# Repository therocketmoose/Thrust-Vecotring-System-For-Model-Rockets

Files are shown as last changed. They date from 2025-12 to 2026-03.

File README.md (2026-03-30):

Thrust Vectoring & Landing Control System for Model Rockets

Lead Engineer: Xavier Vimard
Project Start: 27/09/2025
Expected Completion: 20/05/2026

Project Overview:

This repository contains the full development of a thrust-controlled landing system (TCLS) for a model rocket platform. The project aims to design, build, and test a reusable model rocket capable of performing controlled ascent, attitude stabilization, descent management, and soft landing. The objective is to create a working proof-of-concept that integrates thrust vectoring, aerodynamic control, reaction wheel stabilization, and deployable landing legs into a unified flight system. This project is expected to operate over a one-year development window, with several intermediate prototypes and test campaigns.

The rocket platform itself is not the primary focus, the emphasis is the TCLS hardware, control algorithms, and validation testing necessary to achieve reliable vertical landing.



Project Goals:
- Develop a fully functional thrust vectoring system capable of four-axis gimbal control for ascent and landing.

- Implement a stability assist system using grid fins to manage minor deviations during ascent.

- Design a reaction wheel to counter roll and maintain thrust vector orientation.
as roll stabilization is critical, as uncontrolled roll makes TVC ineffective.

- Engineer deployable landing legs to ensure stable recovery after touchdown.

- Build a complete electronics and software stack integrating sensors, control logic, and closed-loop PID stabilization.

- Validate feasibility via simulation, static fire testing, and full-scale launch tests.

Development Timeline:

My project follows a structured month-by-month roadmap:

- Nov 2025: Design, print and stress test the TVC mount, the reaction wheel and the payload bay.
- Dec 2025: Design and simulate and prepare the code for the PCB.
- Jan 2026: Test the TVC with real motors, sssemble prototype rocket (without parachute), refine TVC mount, begin full system dry runs.
- Feb 2026: First flight test of the prototype, collect IMU/GPS data, evaluate control authority.
- Mar 2026: Analyze flight performance, improve PID tuning, begin landing system integration.
- Apr 2026: Integrate final landing mechanism, conduct ground validations.
- May 2026: Perform full integration test and finalize launch preparation for main flight.
- Jun 2026: Full-system launch and documentation of results.

System Architecture
Core Components:

- MCU: Teensy 4.1 — selected for deterministic real-time control performance.

- IMU: Bosch BMI088 — optimized for high-vibration flight profiles.

- Barometer: MS5611 — high-resolution altitude tracking (10 cm).

- Ground Sation: ESP32 and Lora reciever — supplementary system for communication and logging.

- Structure: Carbon fiber body, TVC gimbal, electronics bay, reaction wheel assembly.



CAD & Mechanical: 
The CAD design includes

- A 4-axis servo-driven TVC module.

- A compact reaction-wheel chamber below the nose cone.

- A payload bay positioned directly above the TVC to avoid cable latency.



Simulation Work

To validate feasibility, ascent and landing behavior is simulated using Xcos (SciLab).
Simulations include gyro stabilization behavior, ascent velocity and altitude curves, and TVC response testing. Early results indicate stable linear altitude growth and adequate thrust-to-weight margin, confirming the motor’s suitability for controlled ascent.



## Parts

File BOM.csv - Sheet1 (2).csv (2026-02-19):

CPN | Part Name | Qty | Source | Mfg Part # | Price | Link
10-2001 | Teensy 4.1 Development Board | 1 | AliExpress | TEENSY41 | 47.59 | https://www.aliexpress.com/w/wholesale-Teensy-4.1-development-board.html
30-0001 | TSP F35-p Rocket Engine (Pack of 2) | 2 | SierraFox | F35-P | 72.5 | https://www.sierrafoxhobbies.com/en/2439-f35-p-single-use-tsp-29-mm-model-rocket-engine-2-pcs.html
20-0001 | BMI088 Shuttle Board | 1 | Mouser | BMI088-SB | 13.67 | https://www.mouser.es/ProductDetail/Bosch-Sensortec/BMI088-Shuttle-Board-30
20-0002 | MS5611 Barometric Pressure Sensor | 1 | ManoMano | MS5611-01BA03 | 7.87 | https://www.manomano.es/componentes-electronicos-4189
20-0003 | LoRa Module SX1278 (433MHz) | 1 | AliExpress | SX1278 | 2.33 | https://www.aliexpress.com/item/1005001593805902.html
30-0002 | 5V DC Motor (Hobby Type) | 1 | AliExpress | Generic | 0.99 | https://www.aliexpress.com/w/wholesale-5v-dc-motor.html
30-0003 | 9g Micro Servo (SG90) (5pcs) | 1 | AliExpress | SG90 | 9.49 | https://www.aliexpress.com/item/32425569444.html
30-0004 | 5g Micro Servo (GH-S37D) | 1 | AliExpress | GH-S37D | 2.89 | https://www.aliexpress.com/item/1005005335388228.html
10-2002 | ESP32-WROOM-32 Dev Module | 1 | AliExpress | ESP32-WROOM | 2.24 | https://es.aliexpress.com/item/1005006096278268.html
20-0004 | SX1278 LoRa Receiver (868MHz) | 1 | AliExpress | SX1276 | 10.59 | https://www.amazon.es/cart/smart-wagon?newItems=9bc834af-a09a-47e9-a199-14235897edb9,1
20-0005 | LoRa/RF Antenna (SMA 868MHz) | 1 | AliExpress | Generic | 1.82 | https://www.aliexpress.com/item/1005002863723277.html
40-0001 | Custom Carbon Fiber Tubes (Est.) | 1 | Custom | Custom | 70 | N/A

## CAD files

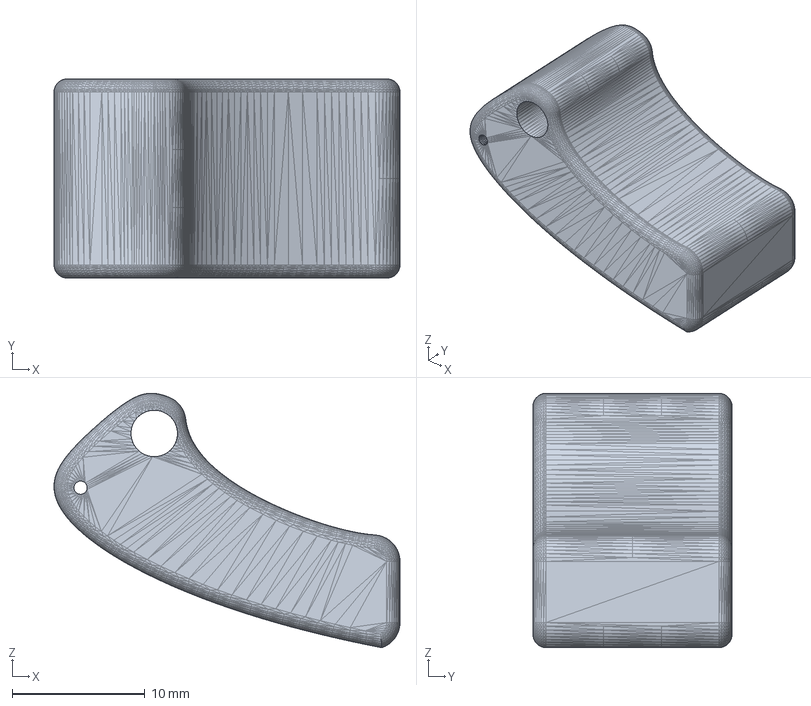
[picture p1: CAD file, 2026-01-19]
3D printing files (TVC)/Thrust arm L.step
26.0 x 15.0 x 19.2 mm

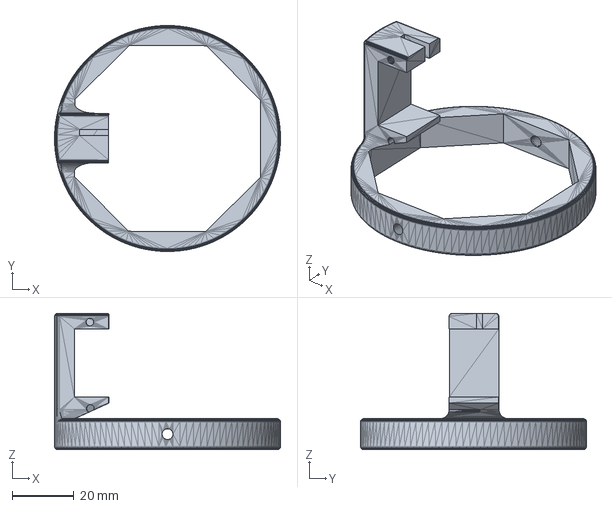
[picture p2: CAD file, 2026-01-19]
3D printing files (TVC)/Outer Gimbal.step
73.0 x 73.0 x 44.0 mm

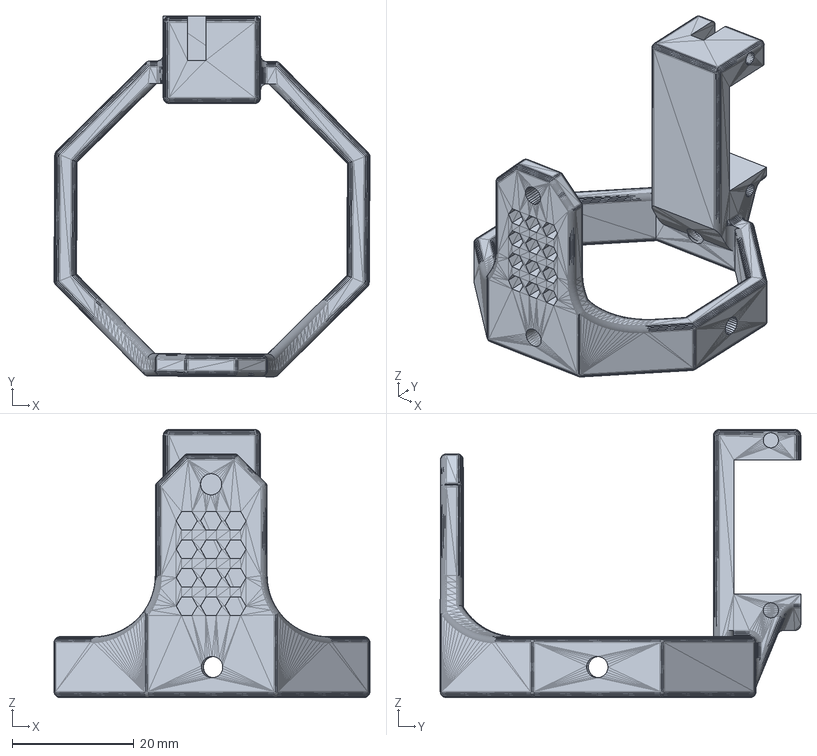
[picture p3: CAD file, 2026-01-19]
3D printing files (TVC)/Inner Gimbal.step
51.9 x 59.2 x 44.0 mm

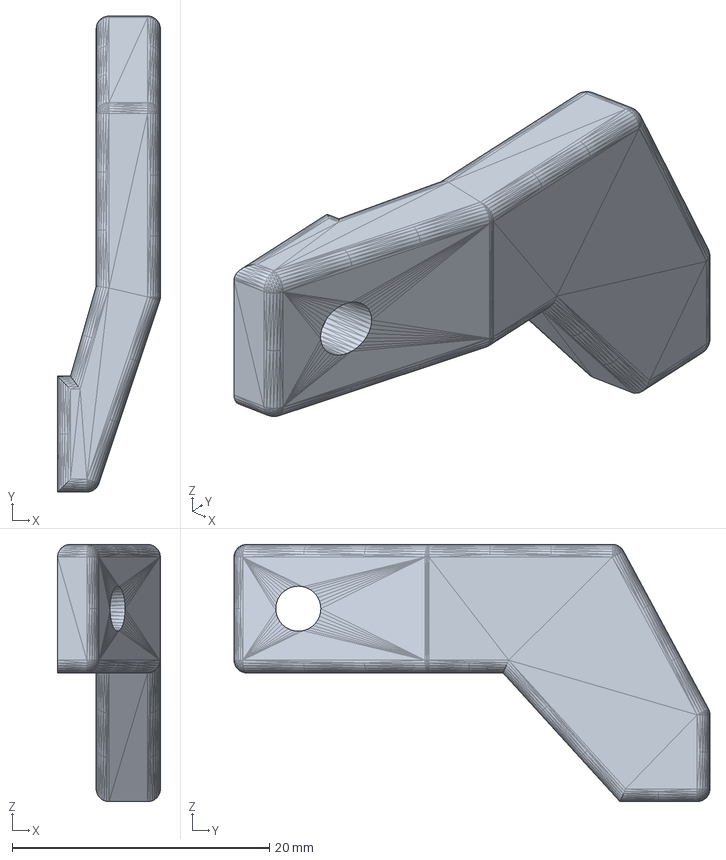
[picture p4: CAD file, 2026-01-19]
3D printing files (TVC)/Pitch Servo Arm.step
8.00 x 37.0 x 20.0 mm

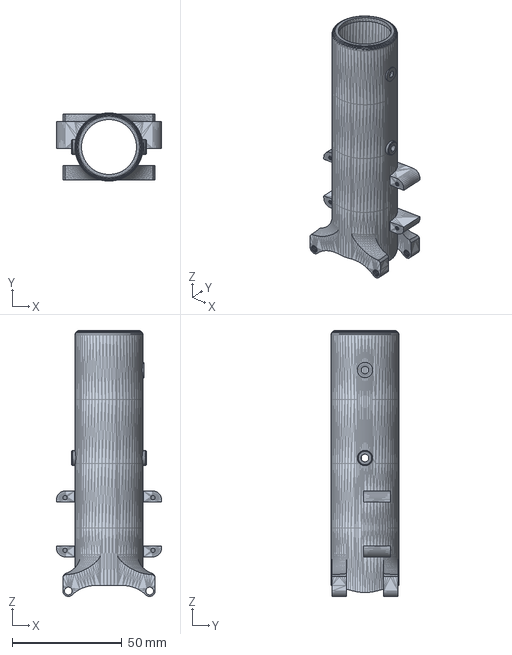
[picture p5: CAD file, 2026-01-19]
3D printing files (TVC)/Motor tube.step
47.9 x 31.0 x 121.0 mm

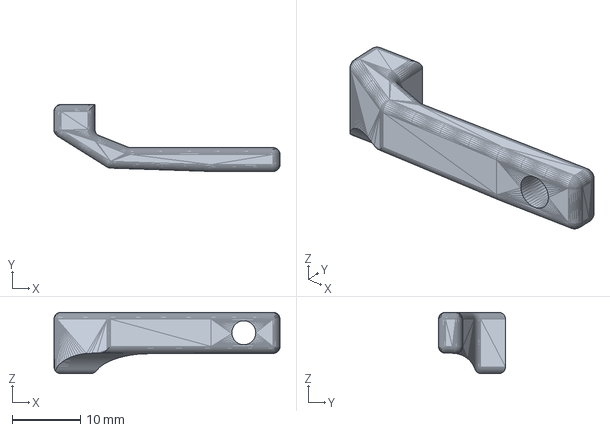
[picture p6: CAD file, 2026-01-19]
3D printing files (TVC)/Yaw Servo Arm.step
33.1 x 9.81 x 9.00 mm

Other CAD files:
3D printing files (TVC)/Thrust arm R.step

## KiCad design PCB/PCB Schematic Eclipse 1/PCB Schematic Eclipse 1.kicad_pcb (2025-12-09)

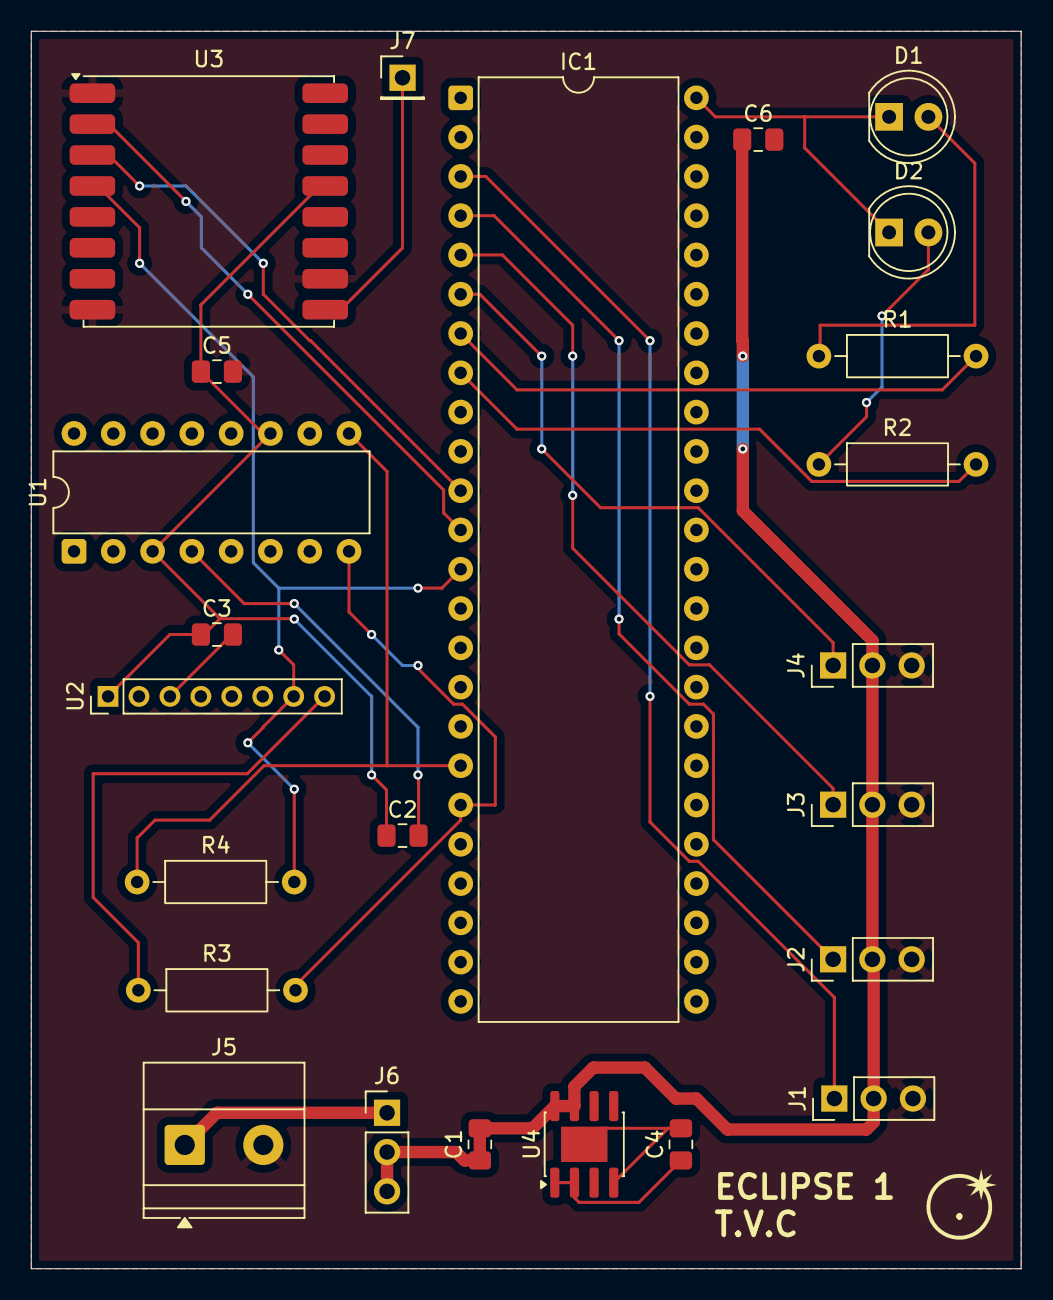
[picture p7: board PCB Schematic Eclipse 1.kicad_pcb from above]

Board: 2 copper layers, 64.0 x 80.0 mm, 25 parts (0 on the bottom side), 24 nets.

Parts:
.: LOGO
C1, C4: C_Polarized; C_0805_2012Metric_Pad1.18x1.45mm_HandSolder
C2, C3, C5, C6: C; C_0805_2012Metric_Pad1.18x1.45mm_HandSolder
D1, D2: LED; LED_D5.0mm
IC1: TEENSY_4.1; DIP-48_W15.24mm
J1, J2, J3, J4, J6: Conn_01x03; PinHeader_1x03_P2.54mm_Vertical
J5: Conn_01x02_Pin; TerminalBlock_Phoenix_MKDS-1,5-2-5.08_1x02_P5.08mm_Horizont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
J7: Conn_01x01_Pin; PinHeader_1x01_P2.54mm_Vertical
R1, R2, R3, R4: R; R_Axial_DIN0207_L6.3mm_D2.5mm_P10.16mm_Horizontal
U1: BMI088; DIP-16_W7.62mm
U2: MS5611-01BA03; PinHeader_1x08_P2.00mm_Vertical
U3: RFM95W-868S2; HOPERF_RFM9XW_SMD
U4: ADP7142ARDZ-3.3; SOIC-8-1EP_3.9x4.9mm_P1.27mm_EP2.29x3mm

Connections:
/I2C_SCL: IC1.19 (A5), R3.2, U1.8 (SCL/SCK)
/I2C_SDA: IC1.18 (A4), R4.1, U1.9 (SDA/SDI)
/SPI_MISO: IC1.12 (MISO), U3.2 (MISO)
/SPI_MOSI: IC1.11 (MOSI), U3.3 (MOSI)
/SPI_SCK: IC1.13 (SCK), R4.2, U2.7 (SDI/SDA), U3.4 (SCK)
/VCC_3V3: C2.1, C3.1, C5.1, U1.3 (VDD), U1.11 (VDDIO), U2.1 (VDD), U3.13 (3_3V)
/Vcc_3V3: C4.1, U4.1 (VOUT), U4.2 (VOUT)
GND: C5.2, J1.3, J2.3, J3.3, J4.3, J5.2, U3.1 (GND), U3.8 (GND@1), U3.10 (GND@2)
unnamed: C4.2, U4.4 (GND), U4.9 (GND)
unnamed: D1.2 (A), R1.1
unnamed: D1.1 (K), D2.1 (K), IC1.48 (GND_2)
unnamed: D2.2 (A), R2.1
unnamed: IC1.4 (BCLK2), J2.1
unnamed: IC1.5 (IN2), J3.1
unnamed: IC1.3 (LRCLK2), J1.1
unnamed: IC1.6 (OUT1D), J4.1
unnamed: IC1.7 (RX2), R1.2
unnamed: IC1.8 (TX2), R2.2
unnamed: J5.1, J6.1
unnamed: J7.1, U3.9 (ANT)
unnamed: C2.2, U1.4 (GNDA)
unnamed: C3.2, U2.3 (GND)
unnamed: R3.1, U2.8 (SCLK)
VCC_5V: C1.1, C1.2, C6.1, J1.2, J2.2, J3.2, J4.2, J6.2, J6.3, U4.7 (VIN), U4.8 (VIN)

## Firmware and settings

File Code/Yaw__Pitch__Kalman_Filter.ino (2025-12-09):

#include <Wire.h>
#include <Servo.h>
#include <SPI.h>
#include <BMI088.h>     // Library: "Bolder Flight Systems BMI088"
#include <MS5611.h>     // Library: "MS5611" by Rob Tillaart
#include <RadioLib.h>   // Library: "RadioLib" by Jan Gromes

// ================================================================
//                       USER CONFIGURATION
// ================================================================

// --- LORA SETTINGS ---
// Frequency: 915.0 (US), 868.0 (EU), 433.0 (Asia)
#define LORA_FREQUENCY 915.0 

// --- SERVO PINS (Teensy 4.1) ---
const int servoPitchPin = 2; 
const int servoYawPin   = 3; 

// --- LORA PINS ---
#define LORA_CS   10
#define LORA_DIO0 4
#define LORA_RST  9
#define LORA_DIO1 5

// --- LAUNCH DETECT ---
// Gravity is 9.8. We set this to 13.0 to detect the gentle F15 liftoff.
const float LAUNCH_THRESHOLD = 13.0; 

// ================================================================
//                       OBJECTS & VARIABLES
// ================================================================

// Sensors
// BMI088 Address: 0x18 (Accel) / 0x68 (Gyro). If fails, try 0x19 / 0x69
Bmi088 bmi(Wire, 0x18, 0x68); 
MS5611 baro(0x77); // Default I2C address for MS5611
SX1276 radio = new Module(LORA_CS, LORA_DIO0, LORA_RST, LORA_DIO1); 

// Servos
Servo servoPitch; 
Servo servoYaw;   

// PID Tuning (Adjust these via Serial if needed)
float KpPitch = 2.5, KiPitch = 0.0, KdPitch = 0.8;
float KpYaw   = 1.5, KiYaw   = 0.0, KdYaw   = 0.0;

// PID Variables
float errorPitch=0, prevErrorPitch=0, integralPitch=0;
float errorYaw=0, prevErrorYaw=0, integralYaw=0;
float derivativePitch=0, derivativeYaw=0;

// Servo Limits
int servoCenterPitch = 90;
int servoCenterYaw   = 90;
int servoMin = 60;
int servoMax = 120;

// Deadband (Don't move servos for tiny errors)
const float deadbandPitch = 1.0;
const float deadbandYaw   = 2.0;

// Timers
unsigned long lastServoUpdate = 0;
const int servoUpdateInterval = 20; // 50Hz update for Servos

unsigned long lastTelemetry = 0;
const int telemetryInterval = 100; // 10Hz LoRa update

unsigned long lastTime = 0;
float elapsedTime;

// State Machine
enum RocketState { IDLE, ARMED, VECTORING, LOCKED };
RocketState state = IDLE; // Starts in Safe Mode

// Orientation Data
float pitchOffset = 0;
float yawOffset   = 0;
float pitchFiltered = 0;
float yawFiltered   = 0;

// ================================================================
//                       KALMAN FILTER
// ================================================================
struct Kalman {
  float Q_angle; float Q_bias; float R_measure; 
  float angle; float bias; float rate;  
  float P[2][2];
};

void kalmanInit(Kalman &k) {
  k.Q_angle = 0.001f; k.Q_bias = 0.003f; k.R_measure = 0.03f;  
  k.angle = 0.0f; k.bias = 0.0f; k.rate = 0.0f;
  k.P[0][0] = 0.0f; k.P[0][1] = 0.0f; k.P[1][0] = 0.0f; k.P[1][1] = 0.0f;
}

float kalmanGetAngle(Kalman &k, float newAngle, float newRate, float dt) {
  k.rate = newRate - k.bias;
  k.angle += dt * k.rate;
  k.P[0][0] += dt * (dt*k.P[1][1] - k.P[0][1] - k.P[1][0] + k.Q_angle);
  k.P[0][1] -= dt * k.P[1][1];
  k.P[1][0] -= dt * k.P[1][1];
  k.P[1][1] += k.Q_bias * dt;
  float S = k.P[0][0] + k.R_measure; 
  float K0 = k.P[0][0] / S;
  float K1 = k.P[1][0] / S;
  float y = newAngle - k.angle;
  k.angle += K0 * y;
  k.bias  += K1 * y;
  float P00_temp = k.P[0][0];
  float P01_temp = k.P[0][1];
  k.P[0][0] -= K0 * P00_temp;
  k.P[0][1] -= K0 * P01_temp;
  k.P[1][0] -= K1 * P00_temp;
  k.P[1][1] -= K1 * P01_temp;
  return k.angle;
}

Kalman kalmanPitch;
Kalman kalmanYaw;

// ================================================================
//                       SETUP
// ================================================================
void setup() {
  Serial.begin(115200);
  Wire.begin();       
  Wire.setClock(400000); // Fast I2C

  // 1. Attach Servos & Center Them
  servoPitch.attach(servoPitchPin);
  servoYaw.attach(servoYawPin);
  servoPitch.write(servoCenterPitch);
  servoYaw.write(servoCenterYaw);

  delay(1000); 

  // 2. Initialize BMI088 (IMU)
  Serial.println("Initializing BMI088...");
  int status = bmi.begin();
  if (status < 0) {
    Serial.println("BMI088 Initialization Failed!");
    Serial.println("Check Wiring or try 0x19 address.");
    while (1);
  }
  // Note: We removed setAccelRange to prevent compilation errors. 
  // The sensor defaults are high performance and will work for F15.

  // 3. Initialize MS5611 (Barometer)
  Serial.println("Initializing Barometer...");
  if (!baro.begin()) {
    Serial.println("Barometer not found (Check wiring). Continuing anyway...");
  }

  // 4. Initialize LoRa
  Serial.println("Initializing LoRa...");
  if (radio.begin(LORA_FREQUENCY) == RADIOLIB_ERR_NONE) {
    Serial.println("LoRa Ready.");
    radio.setOutputPower(20); 
  } else {
    Serial.println("LoRa Failed!");
  }

  // 5. Calibration
  Serial.println("Calibrating IMU (Keep Rocket Still)...");
  float sumPitch=0, sumYaw=0;
  const int samples = 500;
  for(int i=0; i<samples; i++){
    bmi.readSensor();
    float ax = bmi.getAccelX_mss();
    float ay = bmi.getAccelY_mss();
    float az = bmi.getAccelZ_mss();
    float pitch = atan2(ax, sqrt(ay*ay + az*az)) * 180.0/PI;
    float yaw   = atan2(ay, sqrt(ax*ax + az*az)) * 180.0/PI;
    sumPitch += pitch;
    sumYaw   += yaw;
    delay(2);
  }
  pitchOffset = sumPitch / samples;
  yawOffset   = sumYaw / samples;
  
  // 6. Init Kalman Filter
  kalmanInit(kalmanPitch);
  kalmanInit(kalmanYaw);

  // Seed Filter with current angle
  bmi.readSensor();
  float ax = bmi.getAccelX_mss();
  float ay = bmi.getAccelY_mss();
  float az = bmi.getAccelZ_mss();
  kalmanPitch.angle = (atan2(ax, sqrt(ay*ay + az*az)) * 180.0/PI) - pitchOffset;
  kalmanYaw.angle   = (atan2(ay, sqrt(ax*ax + az*az)) * 180.0/PI) - yawOffset;

  lastTime = micros();
  
  // 7. Ready
  state = IDLE; 
  Serial.println("----------------------------------------");
  Serial.println("SYSTEM READY. MODE: IDLE (SAFE).");
  Serial.println("Type 'arm' in Serial Monitor to activate.");
  Serial.println("----------------------------------------");
}

// ================================================================
//                       MAIN LOOP
// ================================================================
void loop() {
  // Time keeping
  unsigned long now = micros();
  elapsedTime = (now - lastTime) / 1000000.0; 
  lastTime = now;
  // Prevent division by zero or huge jumps
  if(elapsedTime <= 0) elapsedTime = 0.001;
  if(elapsedTime > 0.05) elapsedTime = 0.05;

  // --- 1. READ SERIAL COMMANDS ---
  if(Serial.available()){
    String cmd = Serial.readStringUntil('\n');
    cmd.trim();
    
    // Arming Command
    if(cmd.equalsIgnoreCase("arm")){
      if(state == IDLE){
        // Only arm if vertical (+/- 20 deg)
        if(abs(pitchFiltered) < 20.0 && abs(yawFiltered) < 20.0) {
           state = ARMED;
           Serial.println(">>> ROCKET ARMED <<< Waiting for Launch (13 m/s^2)...");
        } else {
           Serial.println("ERROR: Rocket tilted! Cannot Arm.");
        }
      }
    }
    
    // Abort Command
    if(cmd.equalsIgnoreCase("abort")){
      state = IDLE;
      Serial.println("ABORTED! Returning to IDLE.");
    }
  }

  // --- 2. READ SENSORS ---
  bmi.readSensor();
  float ax = bmi.getAccelX_mss();
  float ay = bmi.getAccelY_mss();
  float az = bmi.getAccelZ_mss(); // Z is UP

  // Calculate Accelerometer Angles
  float accPitch = (atan2(ax, sqrt(ay*ay + az*az)) * 180.0/PI) - pitchOffset;
  float accYaw   = (atan2(ay, sqrt(ax*ax + az*az)) * 180.0/PI) - yawOffset;

  // Get Gyro Rates (Rad/s -> Deg/s)
  float gyroPitchRate = bmi.getGyroX_rads() * 180.0/PI; 
  float gyroYawRate   = bmi.getGyroY_rads() * 180.0/PI;

  // --- 3. FILTERING (KALMAN) ---
  pitchFiltered = kalmanGetAngle(kalmanPitch, accPitch, gyroPitchRate, elapsedTime);
  yawFiltered   = kalmanGetAngle(kalmanYaw,   accYaw,   gyroYawRate,   elapsedTime);

  float pitch = pitchFiltered;
  float yaw   = yawFiltered;

  // Deadband
  if(abs(pitch) < deadbandPitch) pitch = 0;
  if(abs(yaw)   < deadbandYaw)   yaw   = 0;

  // --- 4. STATE MACHINE ---
  switch(state){
    case IDLE:
      servoPitch.write(servoCenterPitch);
      servoYaw.write(servoCenterYaw);
      integralPitch = 0;
      integralYaw = 0;
      break;

    case ARMED:
      servoPitch.write(servoCenterPitch);
      servoYaw.write(servoCenterYaw);
      
      // LAUNCH DETECT (Threshold 13 m/s^2 for F15)
      // Check absolute value of Z accel
      if (abs(az) > LAUNCH_THRESHOLD) {
         state = VECTORING;
         Serial.println("LAUNCH DETECTED! TVC ACTIVE!");
      }
      break;

    case VECTORING: 
    { // <--- START CURLY BRACE FOR VECTORING CASE
      // --- PITCH PID ---
      errorPitch = 0 - pitch;
      integralPitch += errorPitch * elapsedTime;
      integralPitch = constrain(integralPitch, -15, 15); // Anti-windup
      derivativePitch = (errorPitch - prevErrorPitch) / elapsedTime;
      
      float outputPitch = (KpPitch * errorPitch) + (KiPitch * integralPitch) + (KdPitch * derivativePitch);
      prevErrorPitch = errorPitch;

      // --- YAW PID ---
      errorYaw = 0 - yaw;
      integralYaw += errorYaw * elapsedTime;
      integralYaw = constrain(integralYaw, -15, 15);
      derivativeYaw = (errorYaw - prevErrorYaw) / elapsedTime;
      
      float outputYaw = (KpYaw * errorYaw) + (KiYaw * integralYaw) + (KdYaw * derivativeYaw);
      prevErrorYaw = errorYaw;

      // --- SERVO MIXING ---
      int servoAnglePitch = constrain(servoCenterPitch + outputPitch, servoMin, servoMax);
      int servoAngleYaw   = constrain(servoCenterYaw   + outputYaw,   servoMin, servoMax);

      // Update Servos (limit update rate to prevent jitter)
      if(millis() - lastServoUpdate >= servoUpdateInterval){
        servoPitch.write(servoAnglePitch);
        servoYaw.write(servoAngleYaw);
        lastServoUpdate = millis();
      }
      break;
    } // <--- END CURLY BRACE FOR VECTORING CASE

    case LOCKED:
      break;
  }

  // --- 5. TELEMETRY (LORA) ---
  if (millis() - lastTelemetry >= telemetryInterval) {
    // Read altitude only when needed (saves CPU time)
    // Formula: 44330 * (1 - (p/p0)^(1/5.255))
    float pressure = baro.getPressure();
    float altitude = 44330.0 * (1.0 - pow(pressure / 1013.25, 0.1903));
    
    String telem = "";
    telem += String(millis()); telem += ",";
    telem += String(pitchFiltered, 2); telem += ",";
    telem += String(yawFiltered, 2); telem += ",";
    telem += String(altitude, 1); telem += ",";
    telem += String(state); // 0=IDLE, 1=ARMED, 2=VECTORING
    
    // Send Packet
    radio.transmit(telem);
    
    lastTelemetry = millis();
  }
}

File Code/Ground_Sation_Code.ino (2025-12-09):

#include <RadioLib.h> // Install "RadioLib" library
#include <SPI.h>

// --- PIN DEFINITIONS (ESP32 Standard VSPI) ---
// Change these if using Arduino Uno/Nano
#define LORA_CS   5
#define LORA_DIO0 2
#define LORA_RST  14
#define LORA_DIO1 4  // Optional, often not needed for basic receive

// Instantiate the radio module
SX1276 radio = new Module(LORA_CS, LORA_DIO0, LORA_RST, LORA_DIO1);

void setup() {
  Serial.begin(115200);
  while (!Serial); // Wait for laptop connection

  Serial.println(F("Initializing Ground Station..."));

  // --- INITIALIZE LORA ---
  // Must match the settings in your Teensy Flight Computer exactly!
  // Frequency: 915.0 (US), 868.0 (EU), 433.0 (Asia/Other)
  int state = radio.begin(915.0); 

  if (state == RADIOLIB_ERR_NONE) {
    Serial.println(F("LoRa Init Success!"));
    
    // Optional: Set spreading factor/bandwidth if you changed them on the rocket
    // radio.setSpreadingFactor(7);
    // radio.setBandwidth(125.0);
  } else {
    Serial.print(F("LoRa Init Failed, code "));
    Serial.println(state);
    while (true);
  }
}

void loop() {
  // Check if a packet has been received
  String receivedData;
  int state = radio.receive(receivedData);

  if (state == RADIOLIB_ERR_NONE) {
    // --- PACKET RECEIVED SUCCESSFULLY ---
    
    // 1. Print the raw data (CSV format from rocket)
    // Format: Time,Pitch,Yaw,Altitude,State
    Serial.print("DATA: ");
    Serial.print(receivedData);

    // 2. Print Signal Strength (RSSI) and Signal-to-Noise (SNR)
    // RSSI: Closer to 0 is better (e.g., -40 is strong, -110 is weak)
    Serial.print(" | RSSI: ");
    Serial.print(radio.getRSSI());
    Serial.print(" dBm");
    
    Serial.print(" | SNR: ");
    Serial.print(radio.getSNR());
    Serial.println(" dB");

  } else if (state == RADIOLIB_ERR_RX_TIMEOUT) {
    // No packet received in this loop, just keep listening
    // This is normal, do nothing.
  } else if (state == RADIOLIB_ERR_CRC_MISMATCH) {
    Serial.println(F("Error: CRC Mismatch (Corrupted Packet)"));
  } else {
    // Some other error
    Serial.print(F("Error: "));
    Serial.println(state);
  }
}

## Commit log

2025-12-04 Add final Pitch-Yaw control code including Kalman Filter files
2025-12-04 Rename Pitch-Yaw Control Code/Yaw__Pitch__Kalman_Filter_copy_20251107115251/Kalman-Filter-Code.ino to Yaw_Pitch_Kalman_Filter/Kalman-Filter-Code.ino
2025-12-09 Full PCB
    [PCB Schematic Eclipse 1-B_Cu.gbl, PCB Schematic Eclipse 1-B_Mask.gbs, PCB Schematic Eclipse 1-B_Paste.gbp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]
2025-12-09 Ground Station Code
2025-12-09 Update Yaw Pitch Code
2025-12-11 Rename Inner Gimbal.stl to Inner Gimbal.stl
    [Inner Gimbal.stl]
2025-12-16 Create Inner Gimbal.stl
    [Inner Gimbal.stl]
2026-01-19 Changed stl files to step
    [Inner Gimbal.step, Inner Gimbal.stl, Motor tube.step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]
2026-01-19 Create Full rocket cad (f3z)
2026-01-19 Create Full rocket CAD
